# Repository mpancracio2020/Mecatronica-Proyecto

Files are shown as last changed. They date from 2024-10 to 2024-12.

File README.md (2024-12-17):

<!-- Improved compatibility of back to top link: See: https://github.com/othneildrew/Best-README-Template/pull/73 -->

<!--
*** Thanks for checking out the Best-README-Template. If you have a suggestion
*** that would make this better, please fork the repo and create a pull request
*** or simply open an issue with the tag "enhancement".
*** Don't forget to give the project a star!
*** Thanks again! Now go create something AMAZING! :D
-->

<!-- PROJECT SHIELDS -->
<!--
*** I'm using markdown "reference style" links for readability.
*** Reference links are enclosed in brackets [ ] instead of parentheses ( ).
*** See the bottom of this document for the declaration of the reference variables
*** for contributors-url, forks-url, etc. This is an optional, concise syntax you may use.
*** https://www.markdownguide.org/basic-syntax/#reference-style-links
-->

# Mecatronica-Proyecto
<!-- [![Contributors][contributors-shield]][contributors-url]
[![Forks][forks-shield]][forks-url]
[![Stargazers][stars-shield]][stars-url]
[![Issues][issues-shield]][issues-url]
[![MIT License][license-shield]][license-url]
[![LinkedIn][linkedin-shield]][linkedin-url]

 -->

<!-- PROJECT LOGO -->
<br />
<div align="center">
  <a href="https://github.com/othneildrew/Best-README-Template">
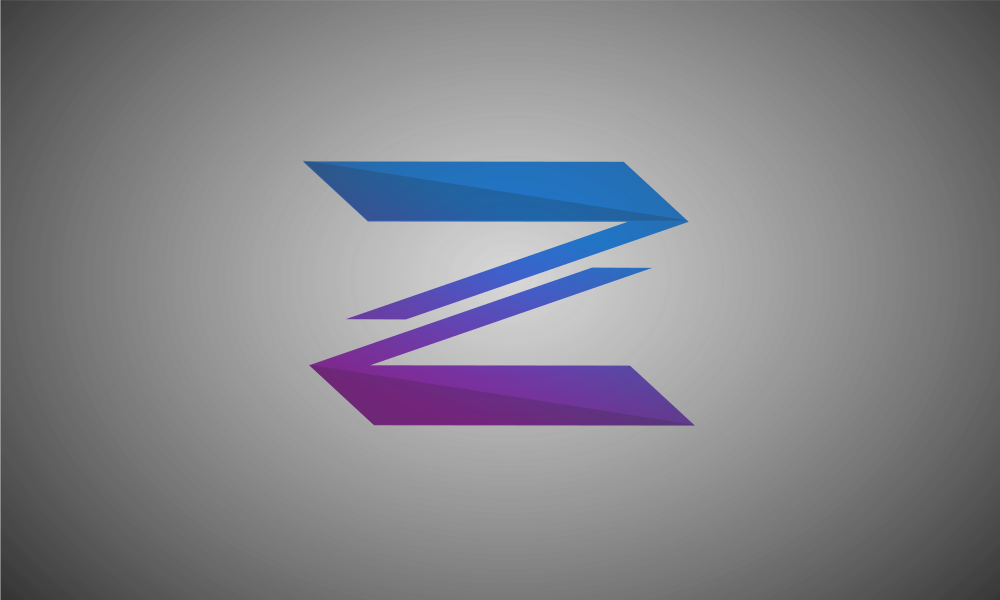
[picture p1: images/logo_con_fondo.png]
    
  </a>

  <h3 align="center">Proyecto-Zeus.</h3>

  <p align="center">
    <br />
    <a href="https://github.com/RoboTech-URJC/Mano-Zeus.git"><strong>Original Robotech Repo »</strong></a>
    <br />
    <br />
    <a href="https://github.com/othneildrew/Best-README-Template">View Demo</a>
    ·
    <a href="https://github.com/othneildrew/Best-README-Template/issues/new?labels=bug&template=bug-report---.md">Personal Blog</a>
  </p>
</div>

---
## **Índice**
1. [Diseño 2D](#id1)
2. [Diseño 3D](#id2)
3. [Diseño Electrónico de la Mano de Zeus](#id3)
4. [Montaje de la Mano de Zeus](#id4)
5. [Código de la Mano de Zeus](#id5)

<div id='id1' />

## Diseño 2D

En estas sesiones nos centramos en el diseño 2D. He aplicado los conocimientos en clase para diseñar un pequeño logo que decore el proyecto.
Requisitos:
* Inkscape.
* Creatividad.

<div align="center">
  <a>
    
  </a>

</div>

A continuacion os dejo un pequeño video de como Marvin ha hecho este pequeño logo sobre el proyecto: 

https://github.com/user-attachments/assets/d4b07c5d-308e-4ce0-a138-df33238a739b

Empleando Inkspace he desarrollado un dibujo de la estructura que debe de tener la mano robótica que vamos a recrear. Es un diseño simple a modo de entendimiento de las diferentes partes que la componen. 

Este es el diseño que hemos obtenido:

<div align="center">
  <a>
    Mano_svg
  </a>

</div>

<p align="right">(<a href="#readme-top">inicio</a>)</p>

En materia del diseño vectorial, también es posible compatibilizarlo con otras técnicas, y para aplicarlo también al proyecto desde otra perspectiva, se me ha ocurrido investigar conversores de gráficos. Existen numerosos convertidores online gratuitos y algunos otros de pago que mejoran los resultados, y esto facilita que ciertas imágenes o diseños puedan ser vectorizados con herramientas también distintas a Inkscape y que no están pensadas en un principio para el diseño vectorial.

Aplicando estas herramientas a nuestro proyecto, Moisés ha diseñado un dibujo simple de algunos componentes de la mano, que también puede servir de apoyo a diagramas explicativos o información que se quiera enseñar y explicar del proyecto:

<p align="center">
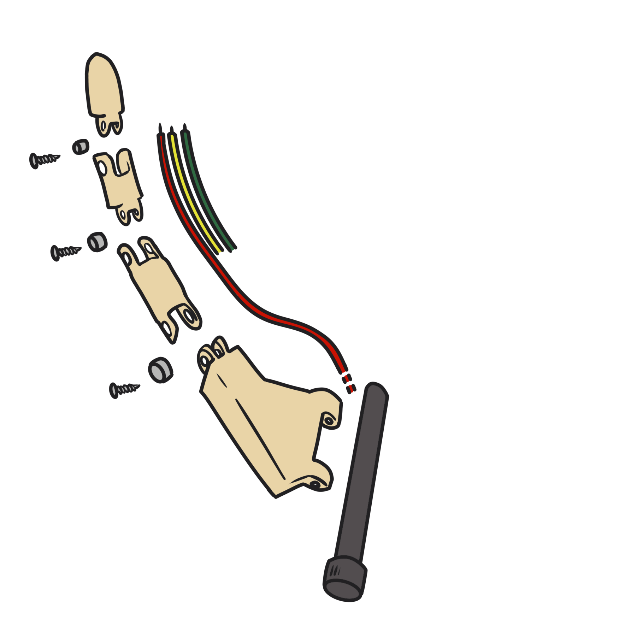
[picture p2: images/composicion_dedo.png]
Alt Imagen 1
  
  Alt Imagen 2
</p>

De las dos imágenes superiores, la izquierda pertenece a un formato en .png, siendo el fichero de dibujo original. Por otra parte la imagen derecha es el resultado de pasar la anterior por un conversor a svg (formato vectorial). El utlizado en este caso ha sido:
- https://png2svg.com/es/

Dejo a continuación un vídeo del proceso de diseño original de la imagen superior, en un programa de diseño no vectorial:

Time-lapse

<div id='id2' />

## **Diseño 3D**

### Mano de Zeus

En cuanto al diseño en 3D que hemos implementado en FreeCad ha sido una estructura simple del ejemplo de dibujo en 2D de Inkspace, obteniendo una estructuracompuesta por rectangulos similar a una mano, pero bastante simplificada. Mostrando en ella todos las piezas en las que tenemos pensado estructurarla.

La estructura se encuentra en el siguiente link: [Mano.FCStd](https://github.com/mpancracio2020/Mecatronica-Proyecto/tree/main/images/Mano.FCStd)

Sin embargo, este modelo 3D era una simplificación del modelo real que queríamos crear y estaba bastante lejos de la complejidad del modelo real que utilizamos. Por lo tanto, me propuse simular una versión más realista del modelo impreso utilizando sus dimensiones para crear un modelo 3D más simple que todos puedan usar y modificar según sus necesidades.

Creé este modelo en FreeCAD utilizando la herramienta "Part" para el diseño 3D general y la herramienta "TechDraw" para elaborar el plano y extraer las medidas.

Aquí están algunas imágenes del modelo que desarrollé, el cual es más similar al real y abarca únicamente la parte de la mano, incluyendo los huecos para pasar los hilos y mover los dedos. La muñeca y el antebrazo no están diseñados.

<p align="center"> 
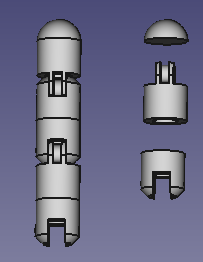
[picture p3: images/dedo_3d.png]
   
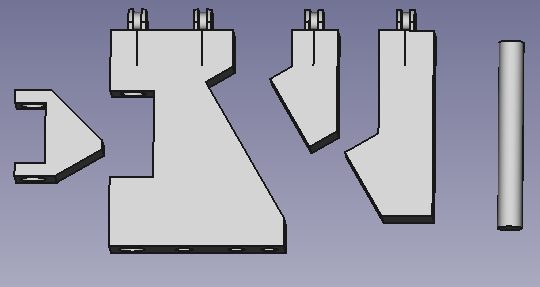
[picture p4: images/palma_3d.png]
   
</p> 
<p align="center"> 
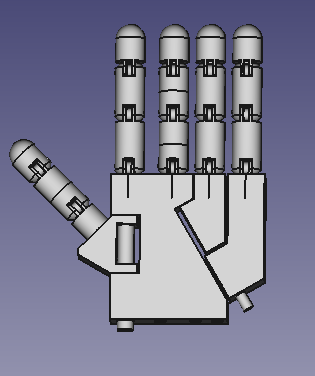
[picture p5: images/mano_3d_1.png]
   
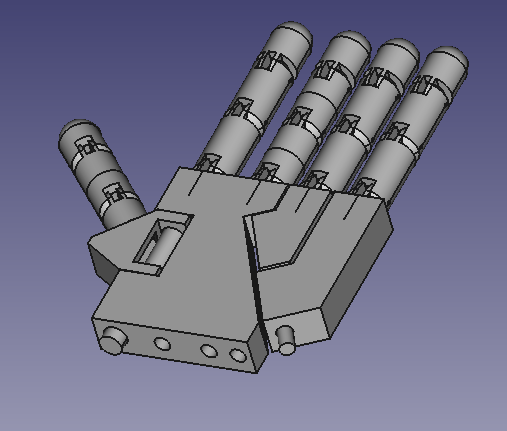
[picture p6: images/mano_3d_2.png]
  
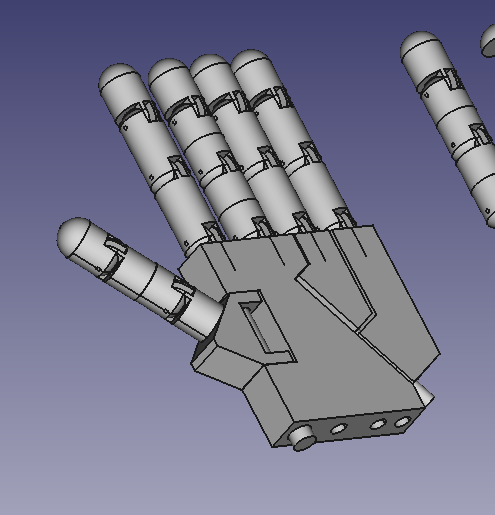
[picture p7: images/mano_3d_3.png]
   
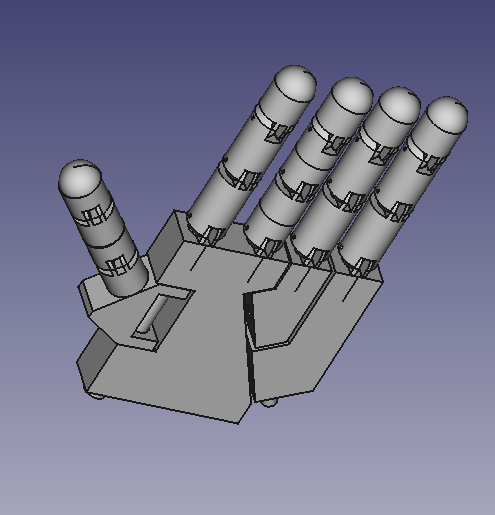
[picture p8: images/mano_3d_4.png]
   
</p>

Este es un video del diseño final.

<p align="center"> 
   
</p>

Los planos de las piezas son los siguiente:

- Dedo:
<p align="center"> 
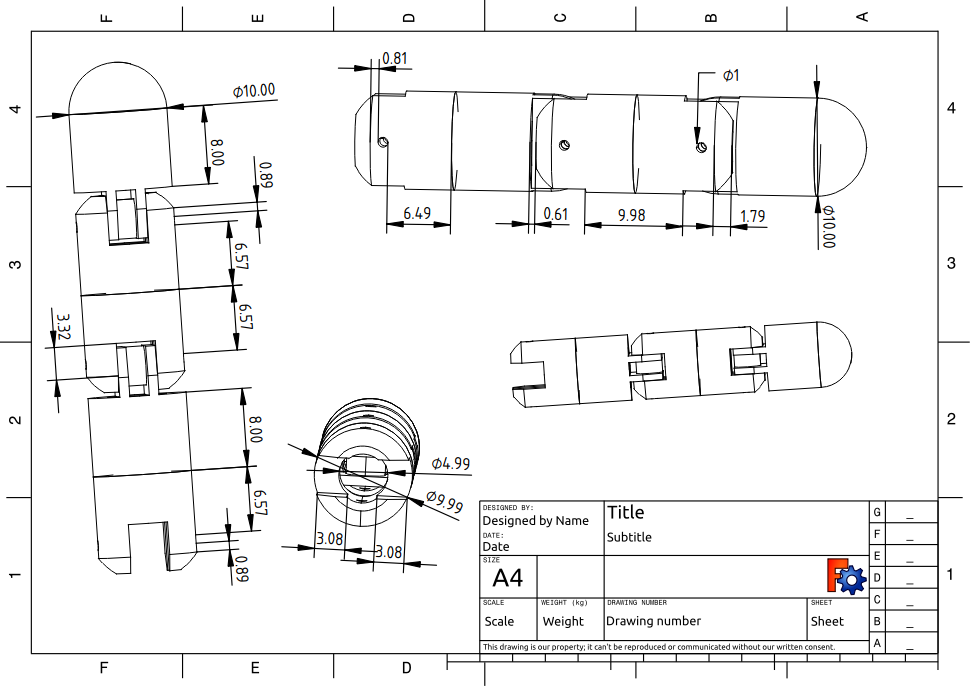
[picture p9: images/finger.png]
   
   
</p>

- Pulgar:
<p align="center">
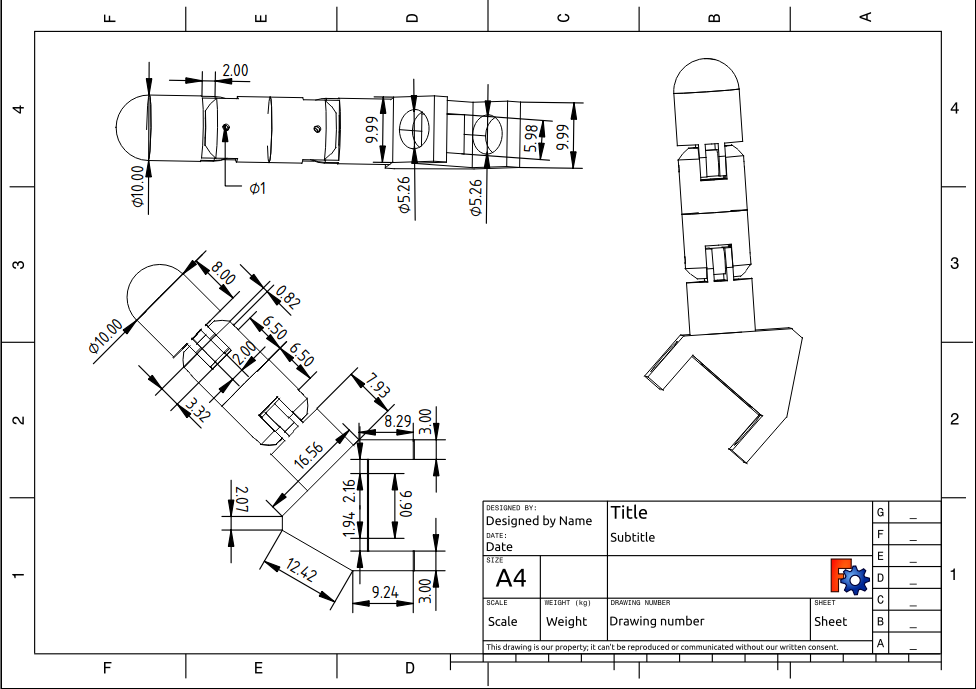
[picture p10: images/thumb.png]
   
   
</p>

- Palma:
<p align="center">
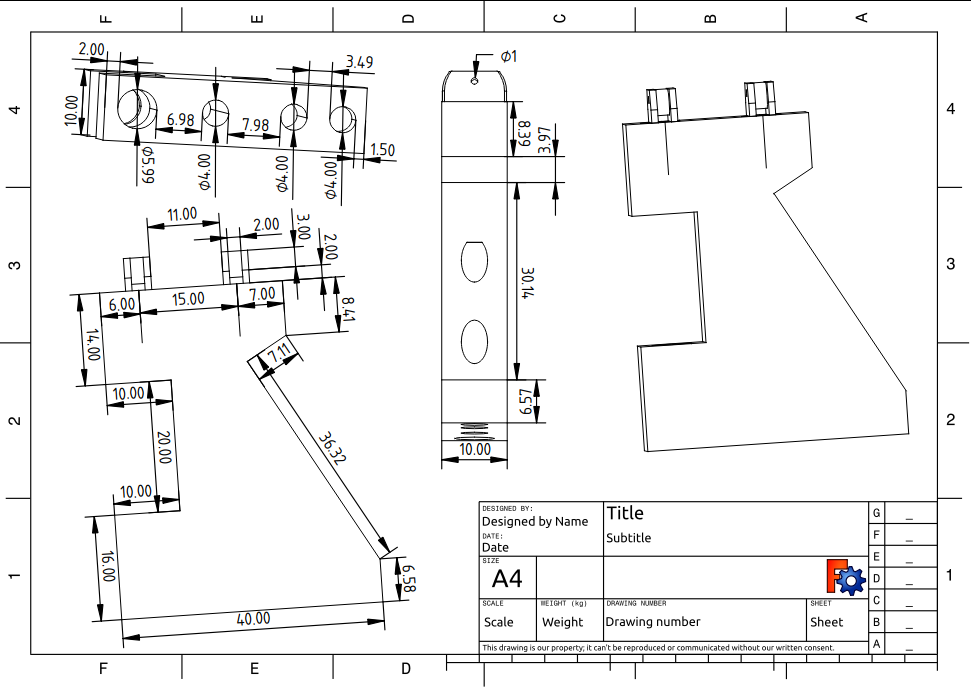
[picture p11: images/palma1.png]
   
   
</p>

- Palma anular:
<p align="center">
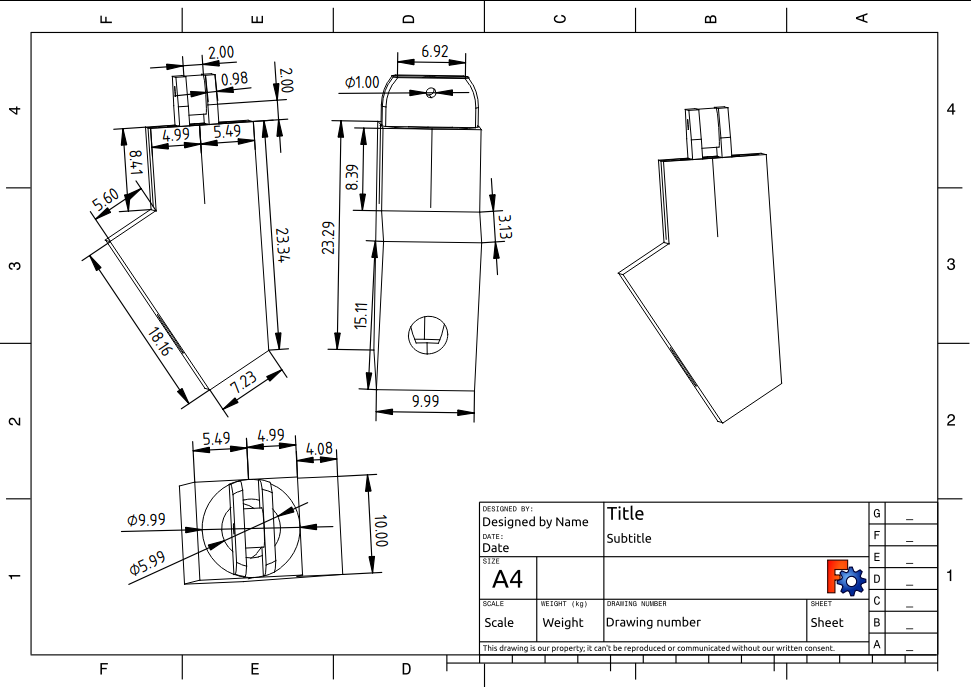
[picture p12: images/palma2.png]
   
   
</p>

- Palma meñique:
<p align="center">
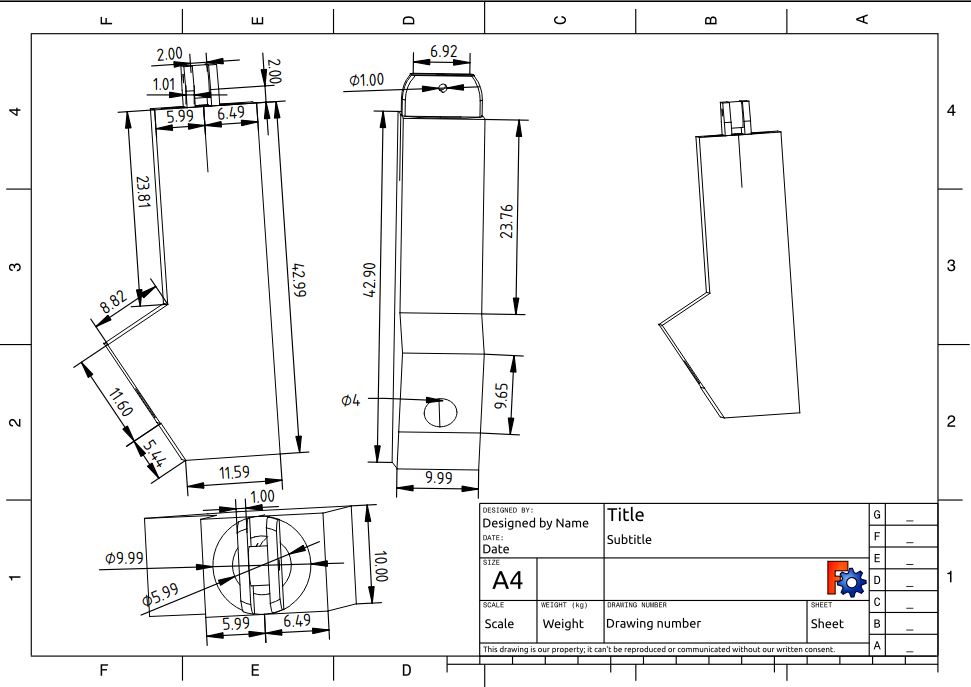
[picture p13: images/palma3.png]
   
   
</p>

- Mano en general:
<p align="center">
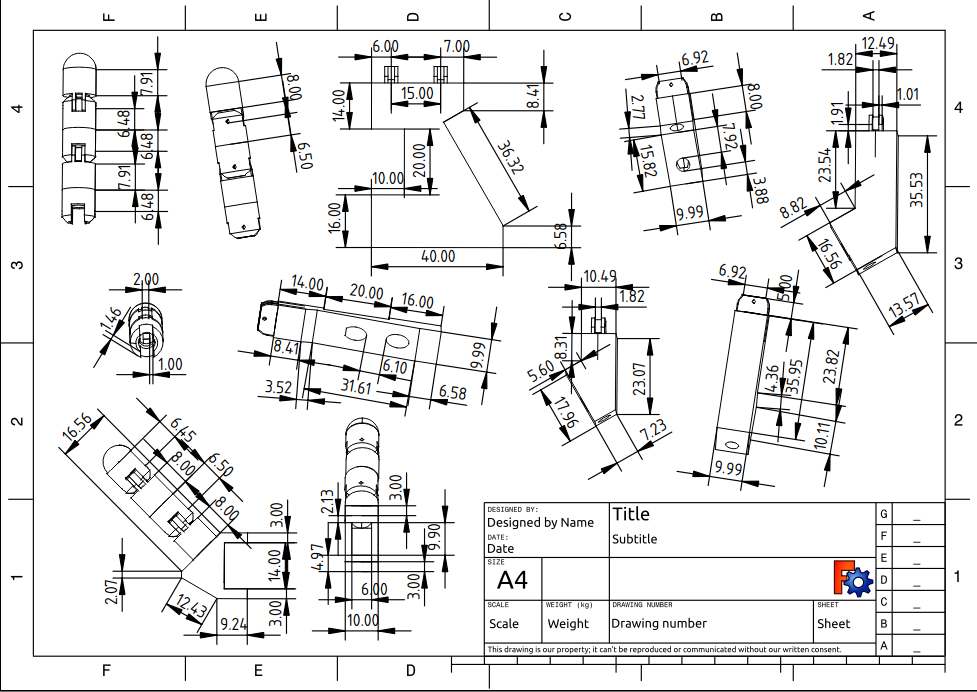
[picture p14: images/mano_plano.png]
   
   
</p>

Y el archivo con todo el diseño 3D lo puedes encontrar en [hand.FCStd](https://github.com/mpancracio2020/Mecatronica-Proyecto/tree/main/images/hand.FCStd)

En cuanto al resto de diseño 3D hemos utilizado Ultimaker Cura para diseñar las piezas basandonos en el proyecto original del cual hemos sacado la idea. Hemos modificado los archivos (.lts) de los componentes aportando diferentes valores para obtener la mejor impresión de las piezas en nuestras impresoras 3D.

### Soporte para el antebrazo

Como parte adicional a la mano de Zeus en sí, decidimos buscar una manera de mantenerla sujeta sin necesidad de apoyarla directamente sobre la mesa, o de sujetarla para cualquier tipo de demostración y presentación. Esto nos llevó a pensar en un soporte que se adaptase a la forma del antebrazo y nos permitiera mantenerlo en posición horizontal, ya que podría ser algo desarrollado en una sola pieza, y más sencillo que un soporte que la mantuviera en vertical a la hora de hacer el diseño. Además, esta posición también resulta más segura, ya que reduce casi al mínimo la posibilidad de que pudiera caerse el conjunto.

Para el soporte, tomando de base un fichero stl, aplicamos ciertas modificaciones realizadas con blender para adaptarlo a nuestras necesidades de tamaño, número de caras y vértices, forma, etc. Las modificaciones aplicadas fueron realizadas utilizando Blender 2.79b, una versión que inicialmente dificulta la compatibilidad con stl, pero que haciendo uso de dos plugins sirvió para aquello que necesitábamos. Dichos plugins quedan a continuación para su descarga y utilización en esta misma versión o similares:

- [blender2ogre.zip](./add-ons/blender2ogre-0.6.0.zip)
- [ImportExporTL-blender.zip](./add-ons/ImportExportTL_blender25x_v0.6.2.zip)

Cualquiera que quiera replicar la utilización debe descargar los ficheros previos como zip, sin extraer su contenido y añadirlos tal cual en el apartado de *"Add-ons"* dentro de la pestaña de *"User Preferences"* en el editor de Blender. Una vez hecho esto, cualquier problema de compatibilidad con ficheros stl debería quedar resuelto, tanto para importar como para exportar este tipo de ficheros.

#### Desarrollo en blender

El desarrollo de nuestra versión final del soporte se hizo aplicando al stl original un ajuste leve en su tamaño, junto a una reducción de la carga de vértices y caras que presentaba la figura original. Finalmente tras dejar una versión final que encajaba con aquello que buscábamos, re-exportamos el trabajo a stl para poder posteriormente tomar las medidas pertinentes en FreeCad del soporte hecho.

<p align="center">
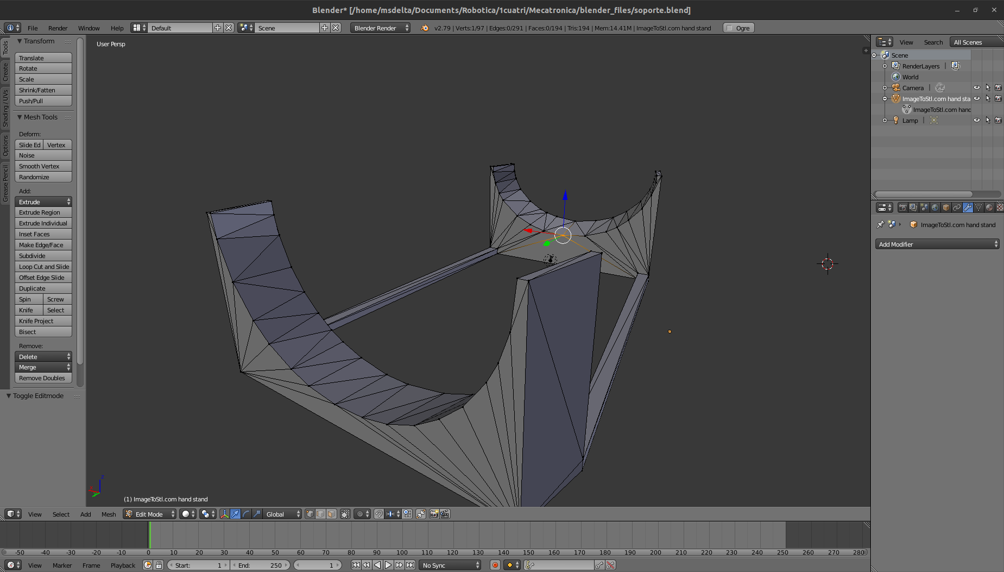
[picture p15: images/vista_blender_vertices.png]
  
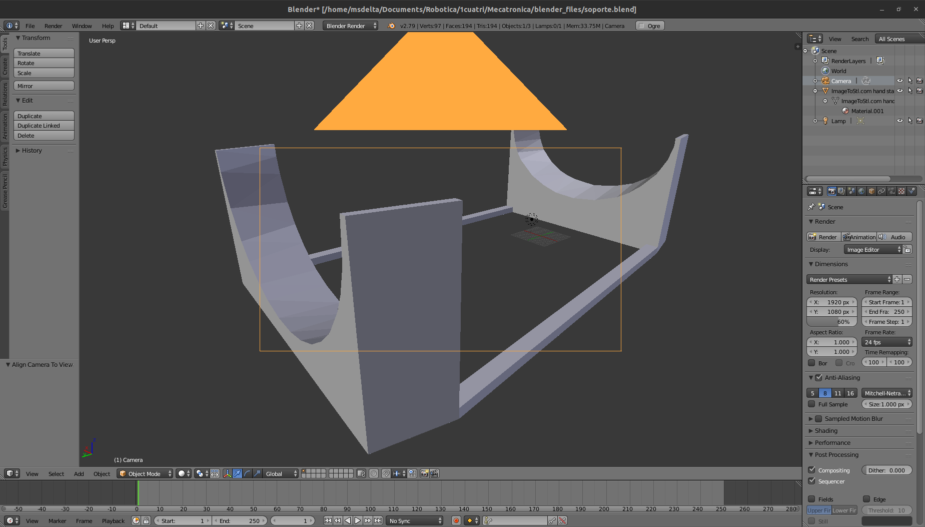
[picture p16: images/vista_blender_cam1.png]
  
</p>

A continuación queda el fichero de blender en su versión final para su copia y libre utilización:

- [Soporte_redu_blend](./models/soporte_redu.blend)

Además de su modelado y ajustado, tratamos de realizar un renderizado del mismo para una mejor presentación y previsualización del resultado final, pero por ciertos problemas con la edición del enfoque de la cámara y los tamaños empleados en edición, no fuimos capaces de lograr un resultado aceptable. Pese a ello, quedan arriba añadidas unas imágenes tomadas del proceso y del modelo visualizado en blender usando distintos modos. Además de las imágenes siguientes, tomadas mientras se intentaba realizar y configurar el renderizado:

<p align="center">
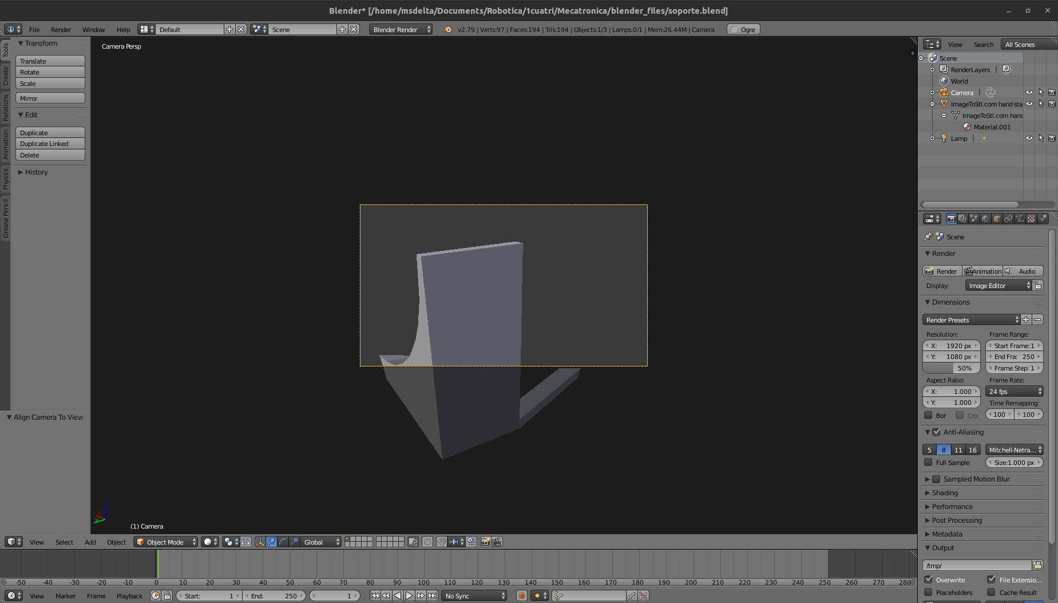
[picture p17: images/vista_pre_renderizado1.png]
  
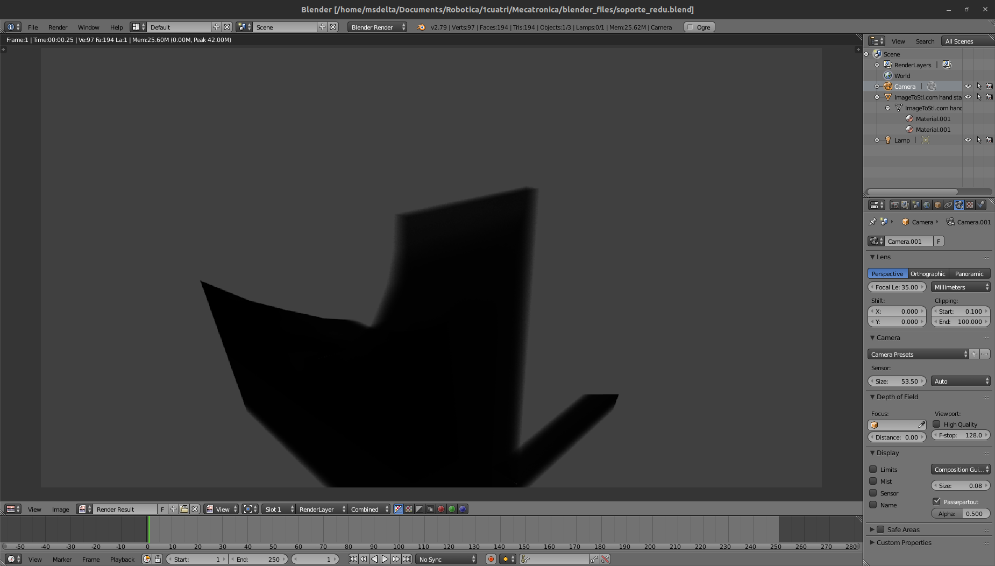
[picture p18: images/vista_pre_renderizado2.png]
  
</p>

Por otro lado, también queda a continnuación el fichero final logrado en formato .stl también para su libre utilización y modificación:

- [Soporte_redu_stl](./models/soporte_redu.stl)

#### Vistas y medidas del soporte

Partiendo del modelo stl logrado finalmente, usamos FreeCad para tomar ciertas medidas del mismo y corroborar su validez, así como para sacar ciertos planos y vistas del mismo.

Dado que el modelo no es simétrico, y tiene algunas irregularidades, por tener que adaptarse necesariamente al antebrazo de la Mano de Zeus, hay ciertas medidas que resultan poco intuitivas y puede creerse que son erróneas, pero si comprobamos todas las vistas y nos fijamos en la orientación de las caras laterales, podemos ver que realmente las medidas son las correctas. 

<p align="center">
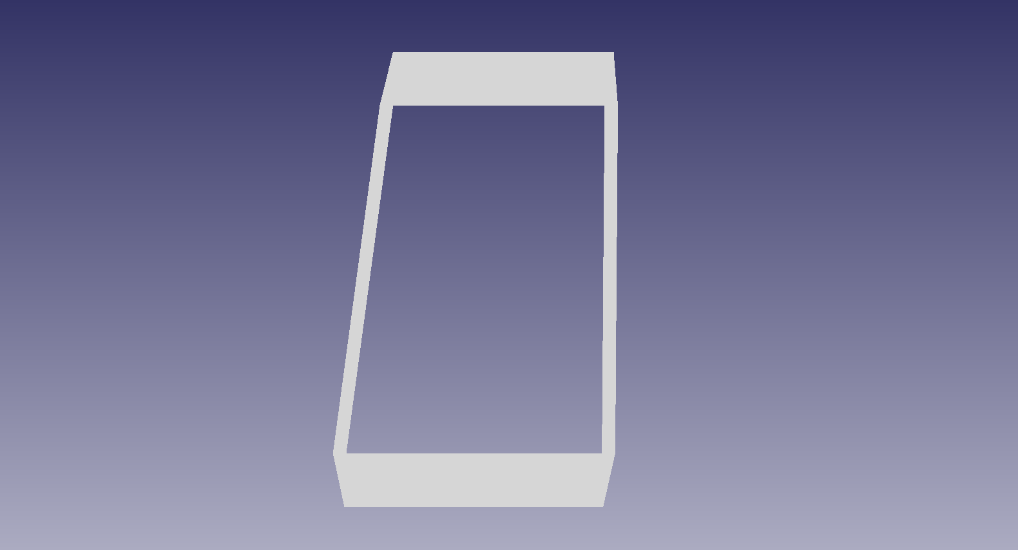
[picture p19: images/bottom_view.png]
bottom_view
  
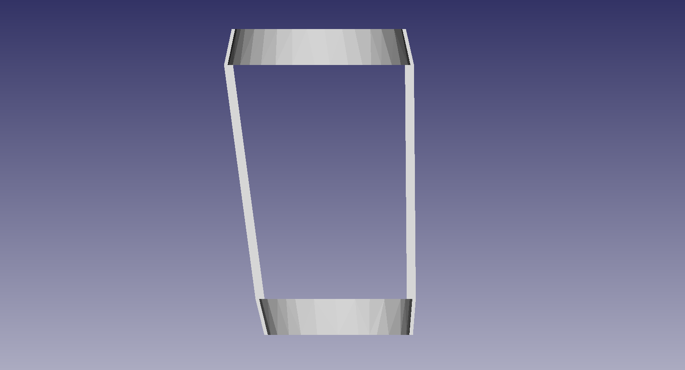
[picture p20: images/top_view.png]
top_view
  
</p>

<p align="center">
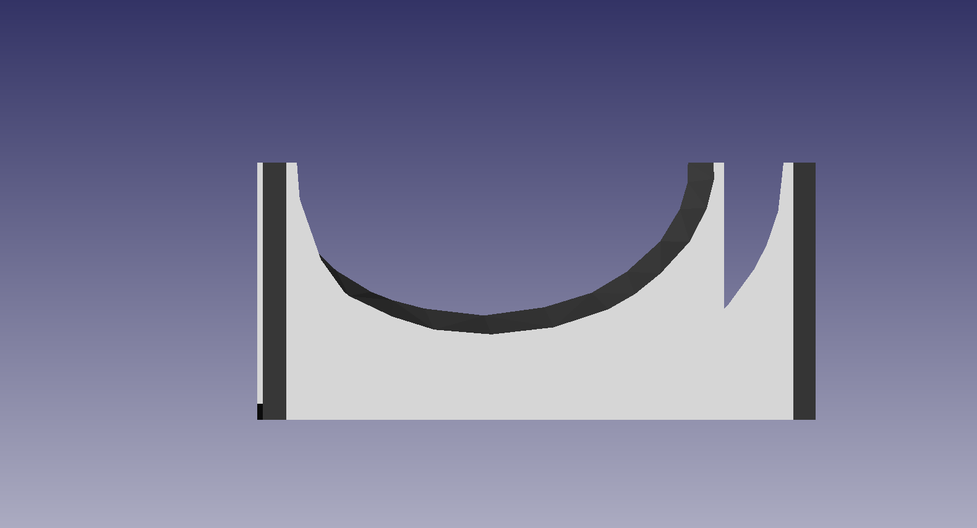
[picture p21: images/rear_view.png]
rear_view
  
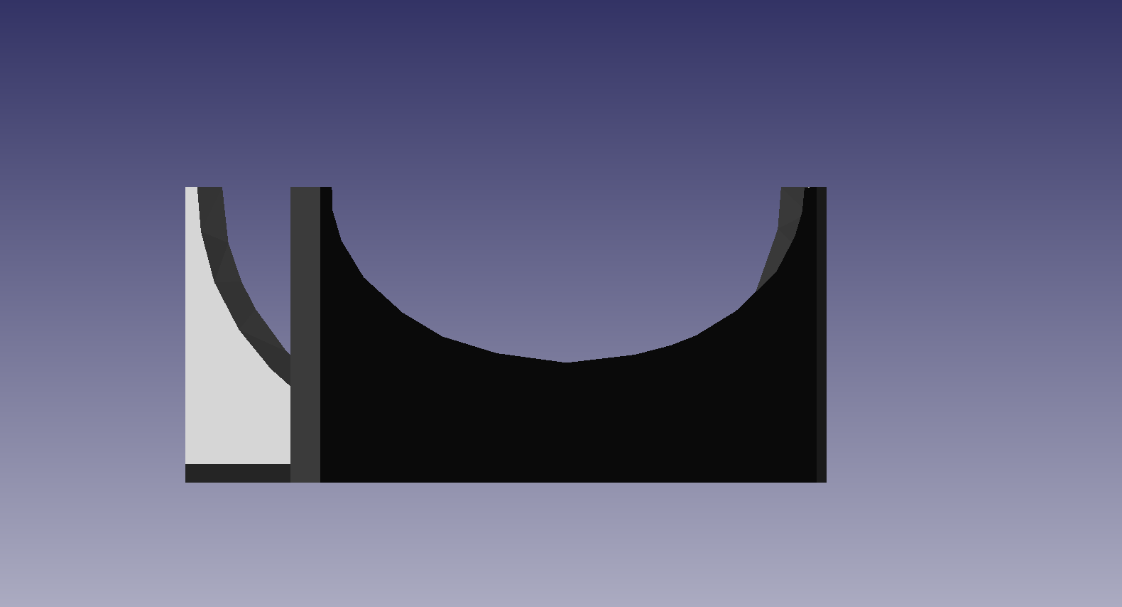
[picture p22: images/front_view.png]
front_view
  
</p>

Las dos imágenes superiores muestran la vista desde la parte inferior y superior (bottom y top) respectivamente de izquierda a derecha, y en igual orden podemos ver las vistas desde la parte trasera y delantera (rear y front) en las imágenes inferiores.

Si comparamos y observamos detenidamente la orientación de los canales laterales que unen los dos arcos sobre los que se apoya finalmente el antebrazo, podemos ver que la pieza carece de simetría, y unido esto a que en las vistas superior e inferior observamos los laterales en detalle, viéndose que no conforman rectas perfectas, facilita la posterior comprensión de las medidas tomadas y las leves irregularidades que parecen presentar en un comienzo.

#### Mediciones laterales

Adicionalmente a lo anterior, dejamos a continuación dos imágenes con las medidas que más dificultad de comprensión pueden tener, las laterales. Estas medidas fueron tomadas de forma persistente usando la función de regla en FreeCad, y pueden servir como idea previa a la visualización de los planos completos finales de la pieza, para hacerse una idea del tamaño y verificar sus dimensiones:

<p align="center">
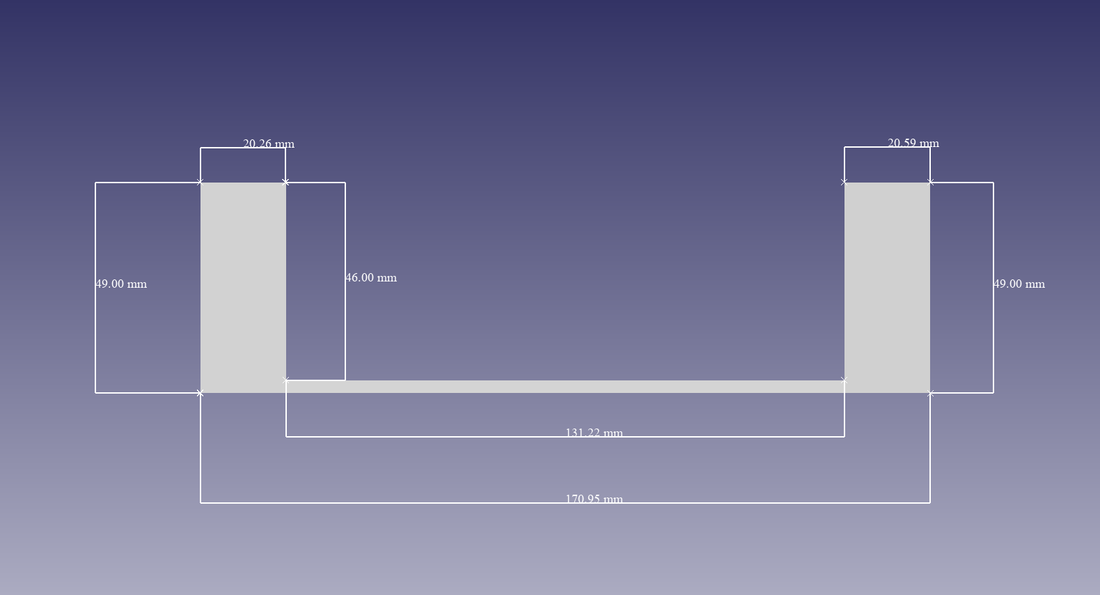
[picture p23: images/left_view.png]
rear_view
  
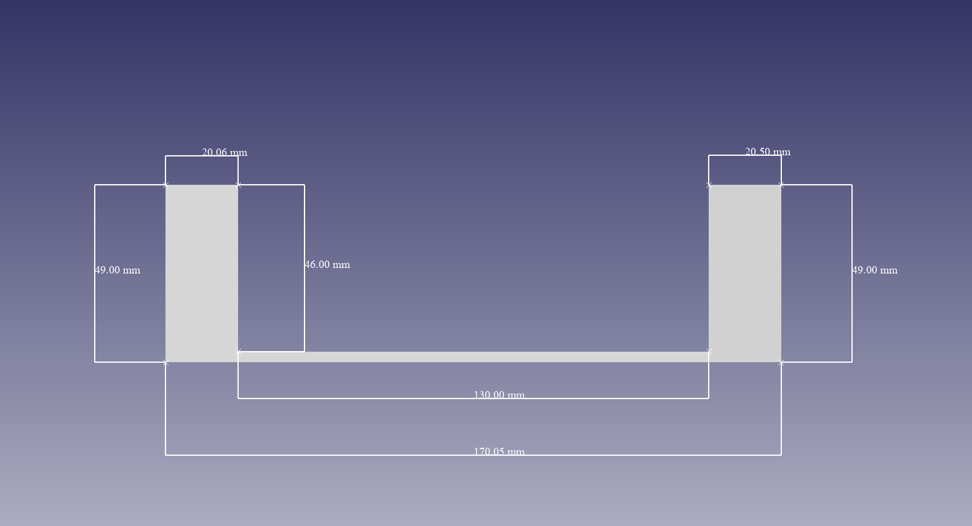
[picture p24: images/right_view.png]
front_view
  
</p>

La imagen izquierda muestra una vista tomada del lado izquierdo del soporte, con las medidas de sus caras más relevantes indicadas en la propia imagen. De igual manera, la imagen derecha muestra la misma información pero relativa a la vista lateral derecha del modelo. 

Y como un extra más a estas imágenes podemos ver una perspectiva diferente que muestra las medidas de ambos lados en una visualización unificada. La imagen inferior está orientada de manera evidencial a las medidas, correspondiendo aquellas en el lado derecho de la imagen con las medidas del lateral derecho:

<p align="center">
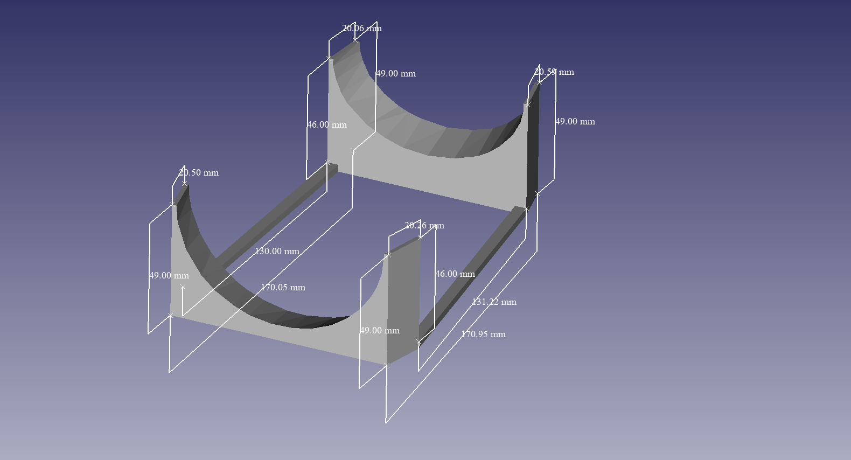
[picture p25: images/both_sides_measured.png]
  
</p>

También queda a continuación el proyecto de FreeCad que hemos empleado para estas mediciones rápidas y explicación de las mismas:

- [Soporte_redu_fcstd](./models/soporte_redu.FCStd)

<p align="center">
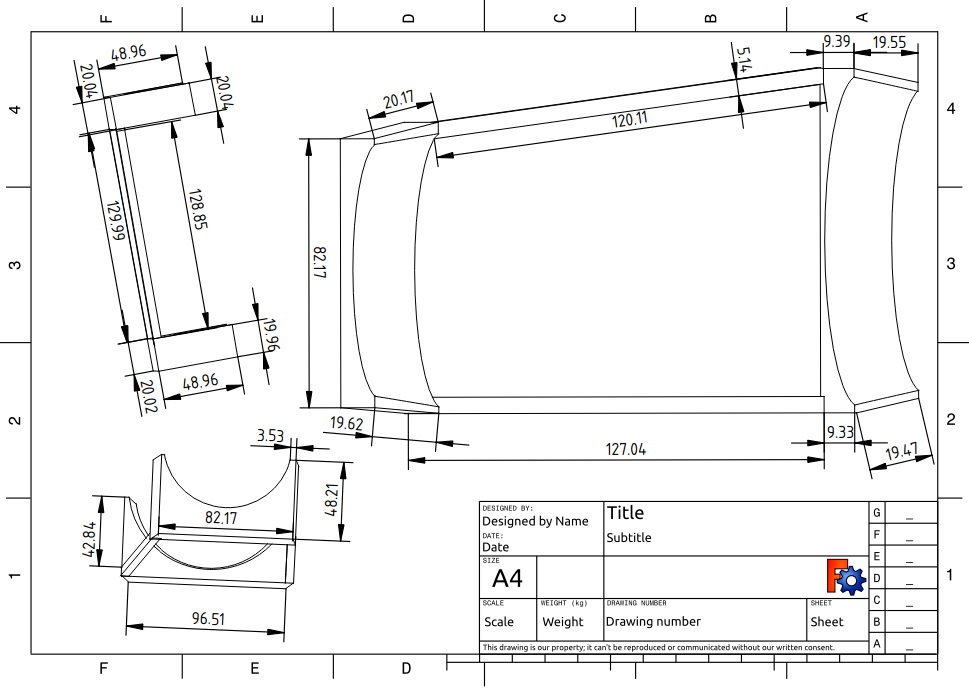
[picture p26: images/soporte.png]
  
  
</p>

<div  id='id3' /> 

## **Diseño Electrónico de la Mano de Zeus**

### Componentes:
Para crear y diseñar el circuito electronico primero debemos elegir que componentes son necesarios y los más óptimos para el correcto funcionamiento de la mano.

- **Arduino UNO / MEGA:** primero hemos elegido como cerebro de nuestro robot un arduino UNO ya que es suficiente para poder comandar el resto de componentes. Si se llega a aumentar el numero de componentes como el añadir otro brazo, usaremos un arduino Mega para poder tener mas pines a los que conectar todos los componentes.

<div align="center">
  <a>
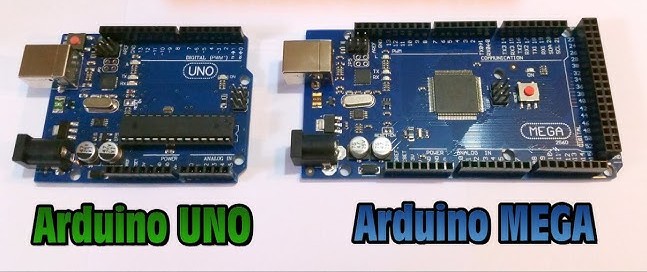
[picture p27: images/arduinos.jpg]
    
  </a>

</div>

- **Servos:** en concreto el modelo tower pro mg996r, un servo de 360 grados el cual nos permite una rotación completa y necesaria para mover los dedos y muñeca los ángulos necesarios. En concreto usaremos 6 servos por cada mano.

<div align="center">
  <a>
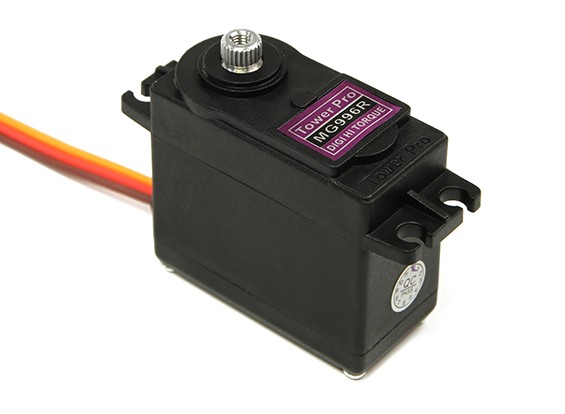
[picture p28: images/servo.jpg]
    
  </a>

</div>

- **Protoboard:** la usaremos para tener mejor conectados y controlados todos los componentes.
- **Cables Macho-Macho / Macho-Hembra:** los usaremos para conectar los componentes entre sí.
- **Batería:** la necesitaremos implementar también para poder mover los servos y que estos puedan mover los dedos.
<div align="center">
  <a>
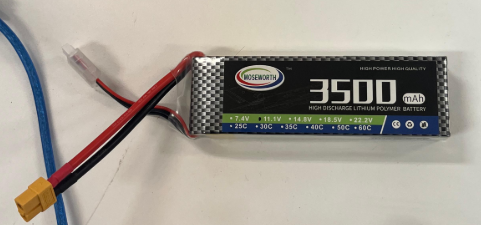
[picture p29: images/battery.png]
    
  </a>
</div>

### Circuito (Fritzing):
Para poder visualizar de una manera mas simple y rapida sin tener que conectar de forma presencial todo el circuito hemos usado la aplicación Fritzing para poder diseñar el circuito. Esta nos permite añadir los componentes necesarios y los modelos específicos que utilizaremos.

El circuito inicial diseñado es el siguiente:

<div align="center">
  <a>
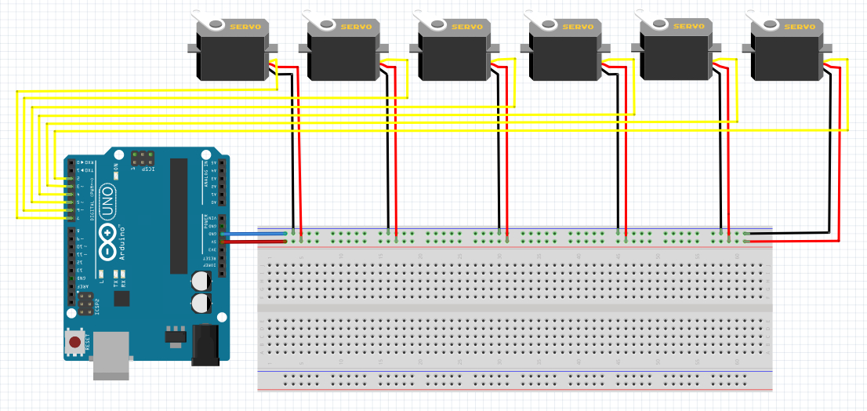
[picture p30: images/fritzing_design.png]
    
  </a>

</div>

Después de probar este circuito nos dimos cuenta de que los servos se movian pero no tenían la fuerza necesaria para poder mover los dedos tirando de los hilos, debido a su peso. Por lo cual se nos ocurrió posteriormente el incluir una batería solo para alimentar a todos los servos. Después de añadirla el circuito diseñado queda de la siguiente forma:

<div align="center">
  <a>
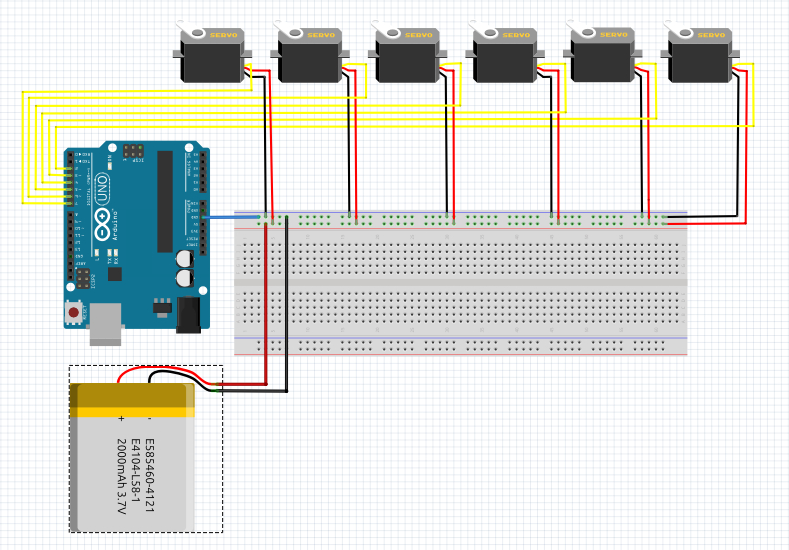
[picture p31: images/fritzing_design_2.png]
    
  </a>

</div>

<div  id='id4' /> 

## Montaje de la Mano de Zeus

### Componentes:

Teniendo el diseño 3d de las piezas, ajustamos adecuadamente los tamaños y utilizamos una impresora 3d para imprimir cada una. En total para la mano derecha desarrollada fueron utilizadas las siguientes partes:
- **Dedo meñique:** conformado por 6 piezas, ensambladas posteriormente entre sí. Adaptado del modelo original: [auriculaire-finger](https://inmoov.fr/inmoov-stl-3d/?bodyparts=Right-Hand&parts=Auriculaire3.stl)
- **Dedo anular:** conformado por 6 piezas, ensambladas posteriormente entre sí. Adaptado del modelo original: [ring-finger](https://inmoov.fr/inmoov-stl-3d/?bodyparts=Right-Hand&parts=ringfinger3.stl)
- **Dedo corazón:** conformado por 6 piezas, ensambladas posteriormente entre sí. Adaptado del modelo original: [majeure-finger](https://inmoov.fr/inmoov-stl-3d/?bodyparts=Right-Hand&parts=Majeure3.stl)
- **Dedo índice:** conformado por 6 piezas, ensambladas posteriormente entre sí. Adaptado del modelo original: [index-finger](https://inmoov.fr/inmoov-stl-3d/?bodyparts=Right-Hand&parts=Index3.stl)
- **Dedo pulgar:** conformado por 6 piezas, ensambladas posteriormente entre sí. Adaptado del modelo original: [thumb-finger](https://inmoov.fr/inmoov-stl-3d/?bodyparts=Right-Hand&parts=thumb5.stl)

<p align="center">
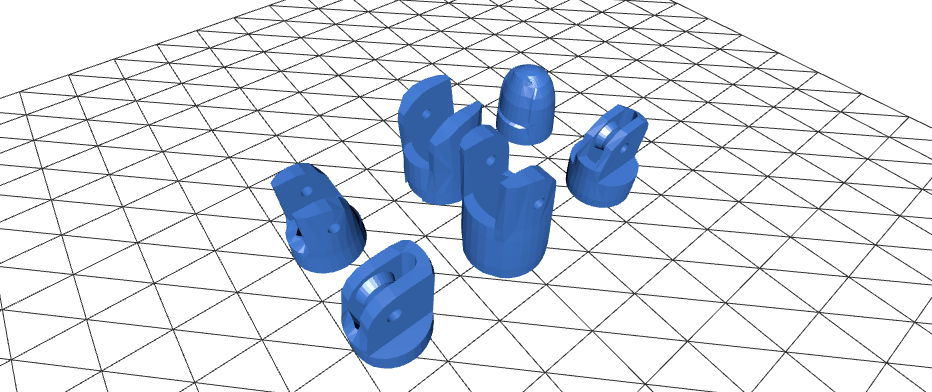
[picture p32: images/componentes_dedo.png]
componentes_dedo
  
</p>

- **Espaciador:** soporte estructural para ensamblar los dedos meñique y anular con la muñeca corta. Adaptado del modelo original: [bolt-entretoise](https://inmoov.fr/inmoov-stl-3d/?bodyparts=Right-Hand&parts=Bolt_entretoise7.stl)
- **Muñeca larga:** pieza única, ensamblada para conformar el mecanismo del movimiento transferido de muñeca a los dedos, junto con la Muñeca corta. Adaptado del modelo original: [wrist-large](https://inmoov.fr/inmoov-stl-3d/?bodyparts=Right-Hand&parts=WristlargeV4.stl)
- **Muñeca corta:** dos piezas, ensambladas al dedo anular y meñique, uniéndolos a la Muñeca larga para conformar el movimiento transferido por la muñeca a los dedos mencionados. Adaptado del modelo original: [wrist-small](https://inmoov.fr/inmoov-stl-3d/?bodyparts=Right-Hand&parts=WristsmallV4.stl)

<p align="center">
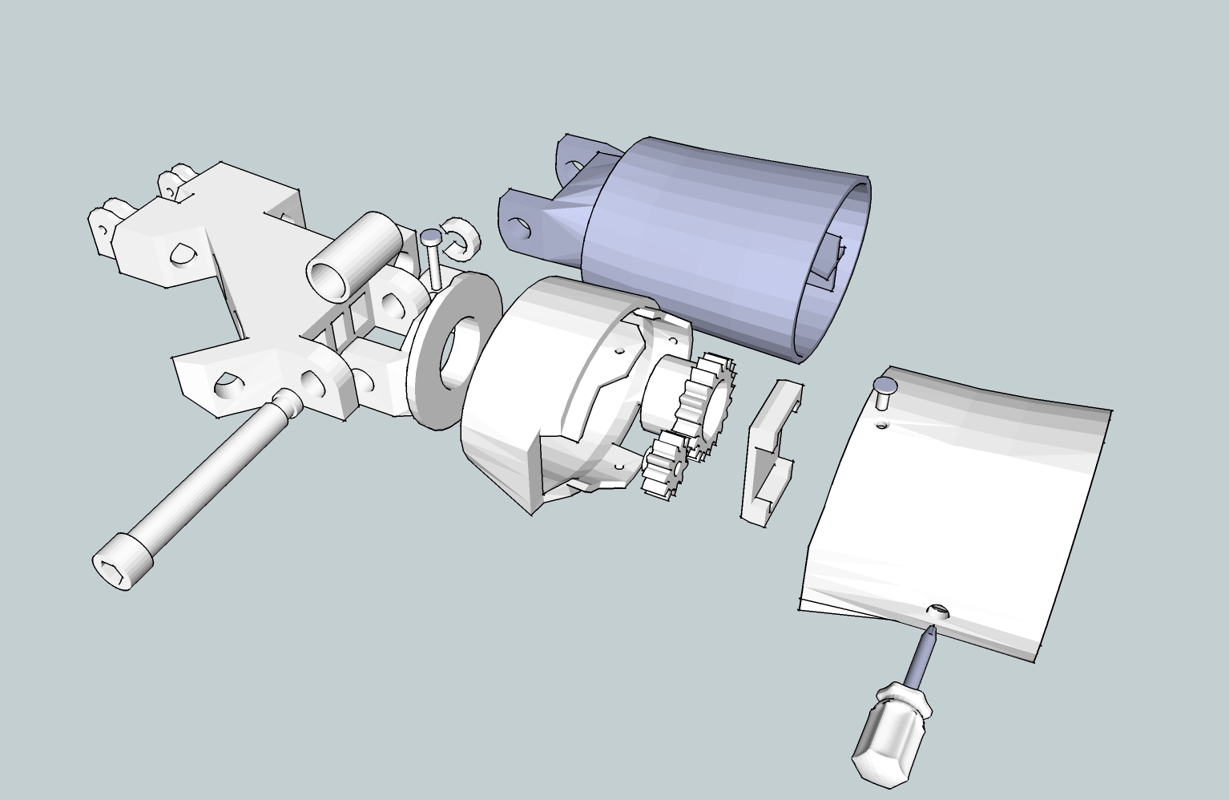
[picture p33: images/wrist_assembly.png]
  
</p>

- **CableHolderWristV5:** elemento de apoyo para facilitar la incorporación del cableado que conecta con muñeca y mano. Adaptado del modelo original: [cable-holder](https://inmoov.fr/inmoov-stl-3d/?bodyparts=Rotation-Wrist&parts=CableHolderWristV5.stl)
- **RotaWrist 3V3:** pieza única relacionada con el módulo de la muñeca. Adaptado del modelo original: [rotawrist3v3](https://inmoov.fr/inmoov-stl-3d/?bodyparts=Rotation-Wrist&parts=RotaWrist3V3.stl)
- **RotaWrist 2V3:** primera de las piezas que conforman la cobertura posterior del módulo de la muñeca. Adaptado del modelo original: [rotawrist2v3](https://inmoov.fr/inmoov-stl-3d/?bodyparts=Rotation-Wrist&parts=RotaWrist2V3.stl)
- **RotaWrist 1V4:** segunda de las piezas que conforman la cobertura posterior del módulo de la muñeca. Adaptado del modelo original: [rotawrist1v4](https://inmoov.fr/inmoov-stl-3d/?bodyparts=Rotation-Wrist&parts=RotaWrist1V4.stl)
- **WristgearsV5:** engranajes necesarios para la rotación del módulo de la muñeca. Adaptado del modelo original: [wrist-gears](https://inmoov.fr/inmoov-stl-3d/?bodyparts=Rotation-Wrist&parts=WristGearsV5.stl)
- **RobocableBackV3:** pieza de apoyo para la integración del cableado, junto con rob-cable-front. Adaptado del modelo original: [rob-cable-back](https://inmoov.fr/inmoov-stl-3d/?bodyparts=Forearm-and-Servo-Bed&parts=RobCableBackV3.stl)
- **RobocableFrontV3v:** segunda pieza de apoyo para la integración del cableado con la rotación de muñeca. Adaptado del modelo original: [rob-cable-front](https://inmoov.fr/inmoov-stl-3d/?bodyparts=Forearm-and-Servo-Bed&parts=RobCableFrontV3.stl)
- **RoboRingV3:** anillos ensamblados a los servomotores, necesarios para implementar el movimiento de los dedos. Adaptado del modelo original: [rob-ring](https://inmoov.fr/inmoov-stl-3d/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)
- **RobServoBedV6:** pieza única empleada para situar correctamente la posición interna de los servomotores. Adaptado del modelo original: [servo-bed](https://inmoov.fr/inmoov-stl-3d/?bodyparts=Forearm-and-Servo-Bed&parts=RobServoBedV6.stl)
- **TensionerRightV1:** pieza de apoyo al ensamblaje de los componentes internos. Adaptado del modelo original: [tensioner-right](https://inmoov.fr/inmoov-stl-3d/?bodyparts=Forearm-and-Servo-Bed&parts=TensionerRightV1.stl)
- **Servo-pulley:** poleas circulares, transforman el movimiento de los servomotores. Adaptado del modelo original: [servo-pulley](https://inmoov.fr/inmoov-stl-3d/?bodyparts=Forearm-and-Servo-Bed&parts=servo-pulleyX5.stl)

<p align="center">
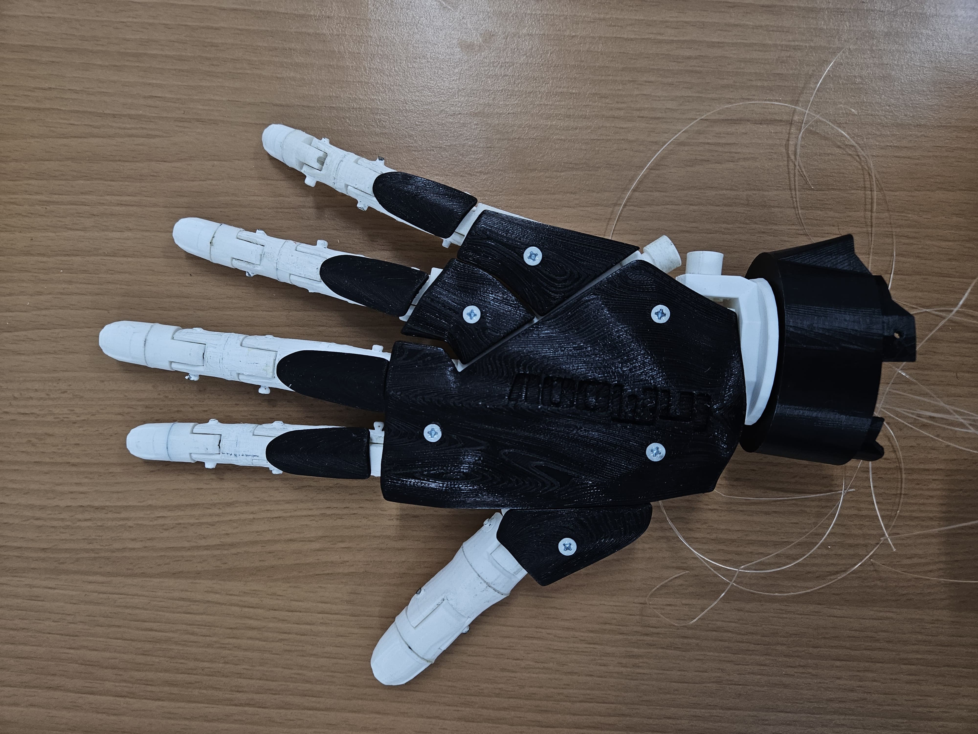
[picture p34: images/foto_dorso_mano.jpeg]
  
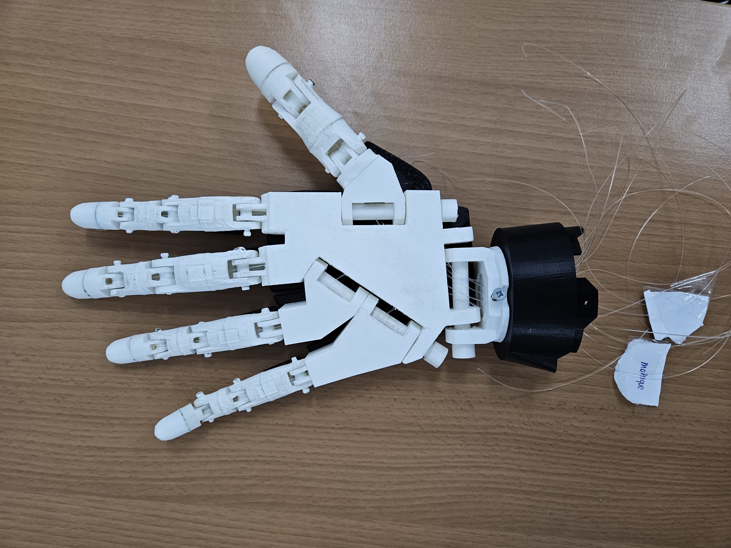
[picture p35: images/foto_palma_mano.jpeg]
  
</p>

- **Cubierta superior (tumbada):** similar a las piezas que cubren los dedos, siendo esta una cobertura para la parte superior de la mano. Adaptado del modelo original: [top-surface](https://inmoov.fr/inmoov-stl-3d/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)
- **Cubrededos:** conformado por 5 piezas, ensambladas sobre los dedos. Adaptado del modelo original: [cover-finger](https://inmoov.fr/inmoov-stl-3d/?bodyparts=Right-Hand&parts=coverfinger1.stl)
- **Soporte Arduino:** pieza única para contener la placa Arduino controladora. Adaptado del modelo original: [arduino-support](https://inmoov.fr/inmoov-stl-3d/?bodyparts=Right-Hand&parts=ardiuinosupport.stl)
- **Robcap3V2:** uno de los componentes que conforman el antebrazo, siendo la cubierta superior del mismo. Adaptado del modelo original: [robcap3v2](https://inmoov.fr/inmoov-stl-3d/?bodyparts=Right-Hand&parts=robcap3V2.stl)
- **Robcap2V4:** primera cubierta anterior del antebrazo. Adaptado del modelo original: [robcap2v4](https://inmoov.fr/inmoov-stl-3d/?bodyparts=Right-Hand&parts=robpart2V4.stl)
- **Robcap3V4:** segunda cubiera anterior del antebrazo. Adaptado del modelo original: [robcap3v4](https://inmoov.fr/inmoov-stl-3d/?bodyparts=Right-Hand&parts=robpart3V4.stl)
- **Robcap4V4:** primera cubierata posterior del antebrazo. Adaptado del modelo original: [robcap4v4](https://inmoov.fr/inmoov-stl-3d/?bodyparts=Right-Hand&parts=robpart4V4.stl)
- **Robcap5V4:** segunda cubierta posterior del antebrazo. Adaptado del modelo original: [robcap5v4](https://inmoov.fr/inmoov-stl-3d/?bodyparts=Right-Hand&parts=robpart5V4.stl)

<p align="center">
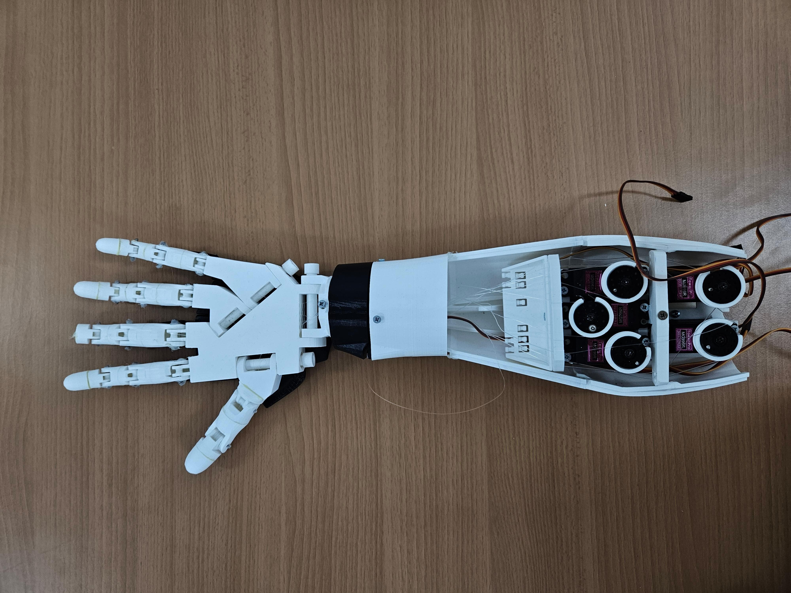
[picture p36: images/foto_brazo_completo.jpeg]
  
</p>

### **Diseño esquemático por componentes**

Para simplificar el montaje, y describir de manera más sencilla la forma en que se realizó, queda a continuación un diagrama dibujado y comentado, con sus elementos explicados en detalle más adelante en este mismo documento:

<div style="display: flex; align-items: left;">

<div style="flex: 1;">
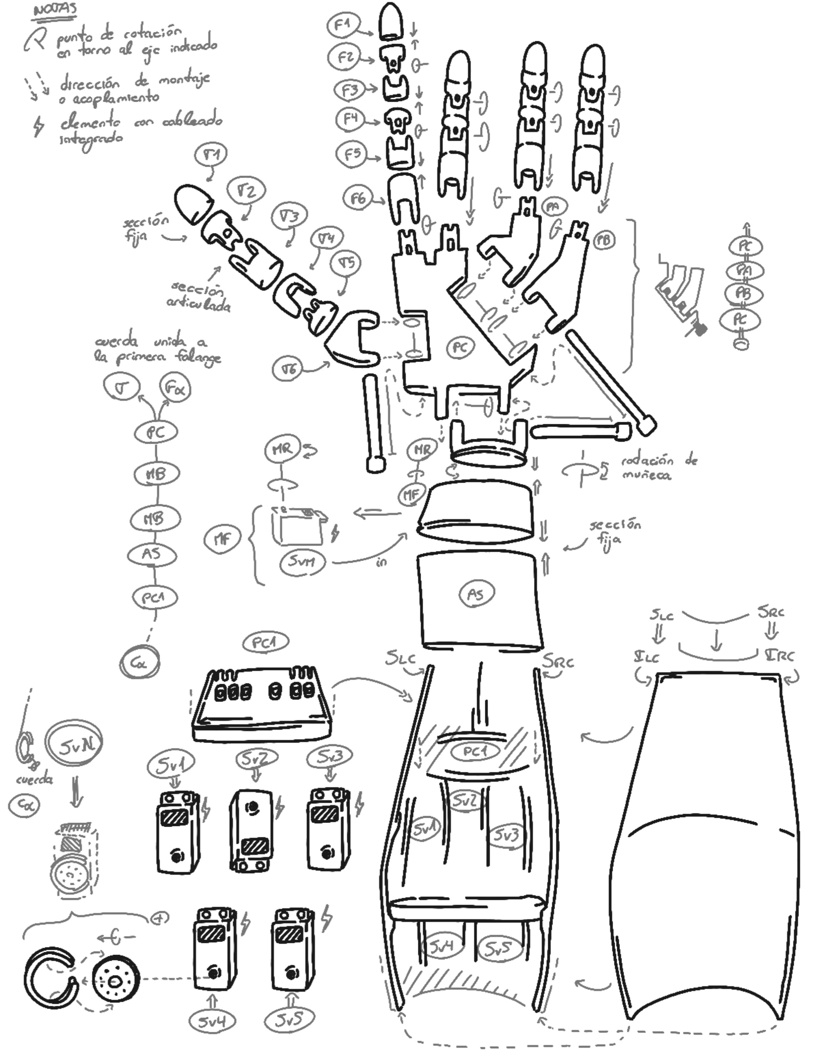
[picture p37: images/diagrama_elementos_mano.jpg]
diagrama

</div>

<div style="flex: 1;">
<table>
  <tr>
    <th>F1 - F6</th>
    <td>Falanges de la superior a inferior, de todo dedo salvo el pulgar</th>
  </tr>
  <tr>
    <th>T1 - T6</td>
    <td>Falanges de la superior a inferior, del dedo pulgar</td>
  </tr>
  <tr>
    <th>PA</td>
    <td>Pieza intermedia entre la parte central de la mano y el dedo anular. Esta pieza rota en torno a un tornillo que la encaja</td>
  </tr>
  <tr>
    <th>PB</td>
    <td>Pieza intermedia entre la parte central de la mano y el dedo meñique. Esta pieza rota en torno a un tornillo que la encaja</td>
  </tr>
  <tr>
    <th>PC</td>
    <td>Pieza central de la mano sobre la cual se ensamblan los dedos pulgar, índice y corazón, y las piezas intermedias PA y PB</td>
  </tr>
  <tr>
    <th>MR</td>
    <td>Parte rotativa de la muñeca, apoyada sobre la muñeca fija, y ofreciendo movimiento en torno al servomotor interno a la misma</td>
  </tr>
  <tr>
    <th>MF</td>
    <td>Muñeca fija, conjunto de piezas y cobertura que sirven de apoyo a la muñeca rotativa para ejercer su giro</td>
  </tr>
  <tr>
    <th>SVM</td>
    <td>Servomotor de la muñeca. Situado interno a la muñeca fija, y anclado a la rotativa</td>
  </tr>
  <tr>
    <th>AS</td>
    <td>Antebrazo superior. Conjunto de piezas encarcasadas más cortas que el antebrazo posterior, uniendo la muñeca con el mismo</td>
  </tr>
  <tr>
    <th>SLC & SRC</td>
    <td>Esquinas superior izquierda (SLC) y superior derecha (SRC) de la carcasa interna del antebrazo posterior o largo. Deben ir alineadas con ILC e IRC respectivamente</td>
  </tr>
  <tr>
    <th>ILC & IRC</td>
    <td>Esquinas superior izquierda (ILC) y superior derecha (IRC) de la carcasa externa del antebrazo largo. La carcasa de la que forman parte se alinea con la previamente mencionada y la recubre, dando forma al antebrazo</td>
  </tr>
  <tr>
    <th>PC1</td>
    <td>Conjunto de piezas centrales al antebrazo largo, ensambladas sobre la carcasa interna para servir de guía para los cables o fibras que mueven los dedos</td>
  </tr>
  <tr>
    <th>SV1 - SV6</td>
    <td>Servomotores numerados del 1 al 6, Componen el sistema de movimiento de los dedos de la mano, uniéndose a ellos por medio de unas cuerdas (C alpha) ancladas a los servos gracias a unas guías circulares</td>
  </tr>
  <tr>
    <th>SVN</td>
    <td>Abreviatura utilizada para referirse a "cualquier servomotor del antebrazo", pudiendo ser desde SV1 hasta SV6 pero no SVM</td>
  </tr>
  <tr>
    <th>C alpha</td>
    <td>Abreviatura utilizada para referirse a "cualquier cuerda ó fibra encargada de guiar el movimiento de los dedos desde su unión a un servomotor SVN" </td>
  </tr>
</table>
</div>

</div>

Aunque en el diagrama aparecen indicados también una serie de elementos que forman parte del dibujo, y la guía puede ser de ayuda para entender las abreviaturas, hay algunas cosas más que hay que tener en cuenta relativas al montaje: 
- Cada dedo está dividido en el mismo número de falanges, y cada falange cuenta con uniones tanto fijas como rotativas, indicadas estas últimas con un icono explicativo en la imagen superior.
- Las falanges de los dedos, tanto pulgar como índice, corazón, anular y meñique, cuentan con guías para los cables en las uniones articuladas, y con aberturas en aquellas uniones fijas, para que sea posible la unión entre la parte final de cada dedo y el servomotor que lo controlará.
- Además de los tornillos de ensamblaje que se han dibujado arriba, el montaje requirió de la utilización de otros tornillos metálicos no indicados previamente, así como algunos elementos adicionales para la correcta sujeción de algunas piezas.
- La parte interior del antebrazo largo, así como el antebrazo superior en detalle, que se indican previamente y se encuentran explicados, cuentan con otros elementos internos en su estructura, no mencionados por no ser de especial relevancia para la comprensión del funcionamiento del sistema mecánico que conforma la Mano de Zeus

### Esquematización

Queda a continuación un breve time lapse de la **parte final** del diseño del esquema superior:

time-lapse

### Impresión y ensamblaje

* Primeras impresiones.

A continuación se muestran la imagenes de las primeras impresiones de los ficheros stl que nos proporciona el proyecto original.

<div align="center">
  <a>
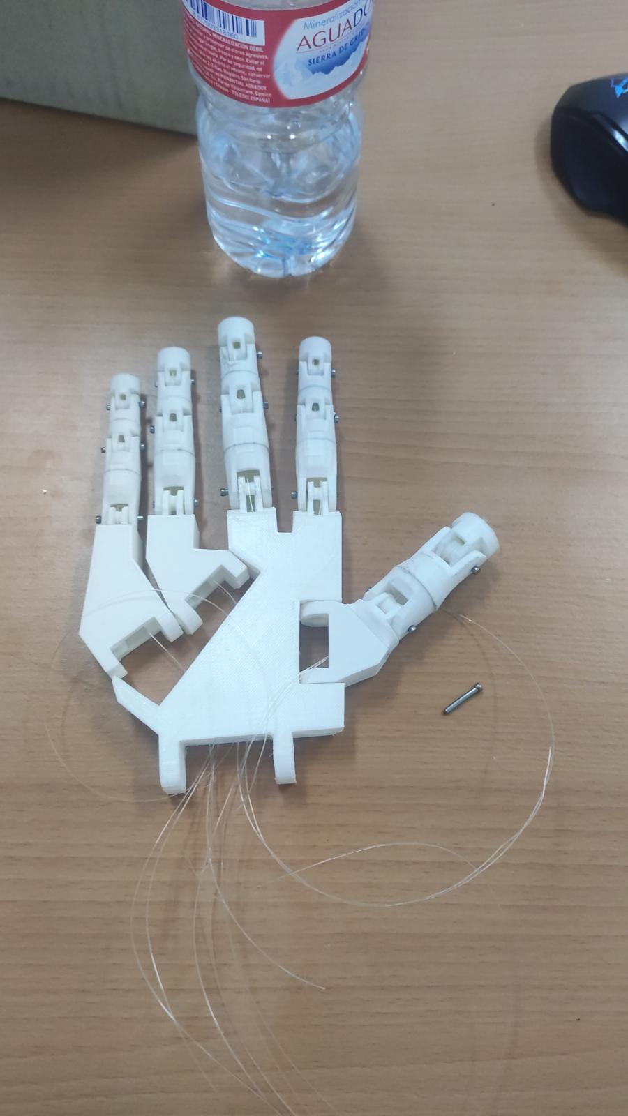
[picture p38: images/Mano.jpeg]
    
  </a>
 <a>
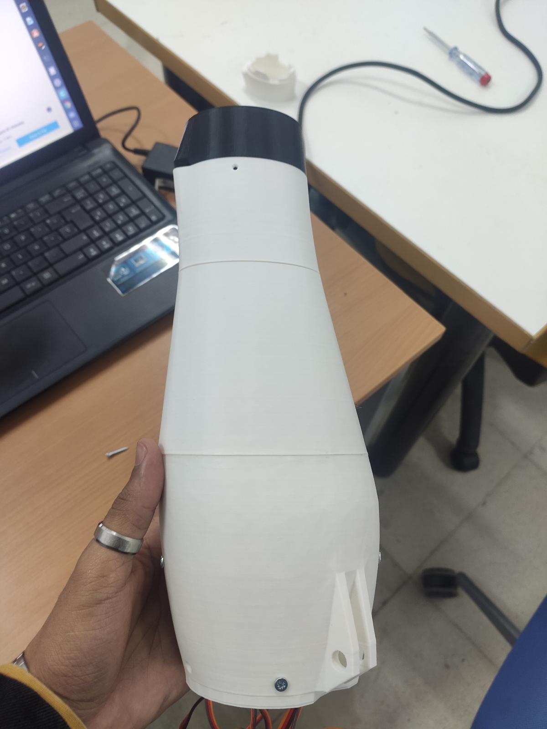
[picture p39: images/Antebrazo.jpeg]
    
  </a>
 <a>
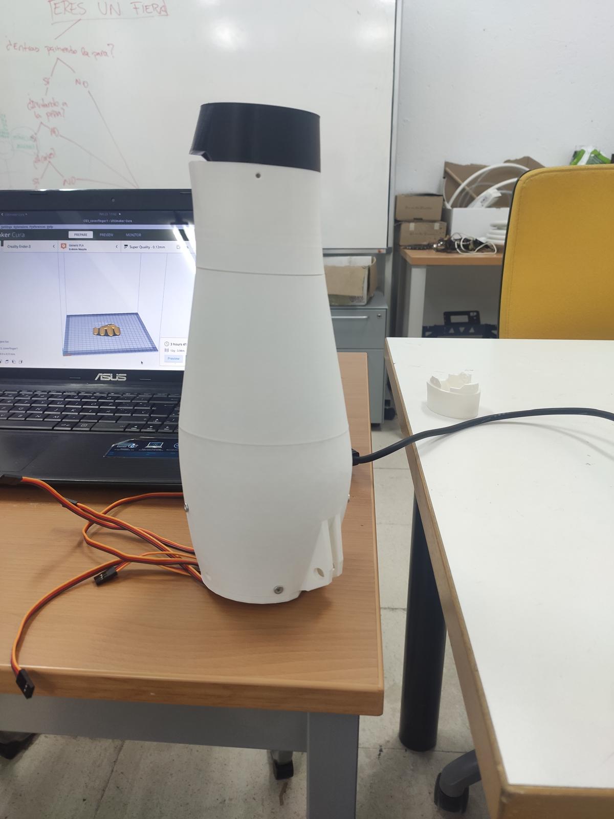
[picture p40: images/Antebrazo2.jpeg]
    
  </a>
 <a>
    
  </a>
  <a>
    
  </a>
  <a>
    
  </a>

</div>
La totalidad de las impresiones de han hecho en una impresora <a href="https://www.creality.com/es/products/ender-3-3d-printer"><strong>Creality Ender 3 »</strong></a>

* Problemas y dificultades.

El mayor problema de todos a la hora de montar las piezas es el material de las mismas, PLA. Esto provocaba que a la hora de encajar o generar una fuerza sobre ellas que no estaba
preparada para soportar, rompiamos la pieza. Han sido varias las piezas que se han vuelto a imprimir debido a roturas. 

Hay que tener en cuenta que hay muchas fricciones y tensiones simultaneas en el mecanismo completo de una sola mano, un total de 6 servos independientes que actuan para cada dedo y muñeca,
que esto funcione acorde es bastante importante, debido a que un minimo error puede provocar las roturas mencionadas anteriormente.

<div  id='id5' /> 

## Código de la Mano de Zeus

El código de la mano esta desarrollado en tres lenguajes, en C++, en Arduino y en Python. 

### Instalación 

Para que funcione correctamente el programa es necesario instalar previamente algunas librerías, a parte de los lenguajes usados.

Librerías utilizadas:

| Librerías | Comando de terminal  | Utilidad
|:--- |:---:| :---|
| numpy | pip install numpy | crear y usar vectores
| tkinter | pip install tkinter | crear una interfaz interactiva
| mediapipe | pip install mediapipe | detectar cuerpos, brazos y manos
| pillow | pip install pillow | procesar imagenes |

En cuanto al desarrollo del código de la mano, lo hemos dividido en varias partes:

### Movimiento

La primera de las partes es el movimiento de la mano. En esta, solo nos centramos en producir el movimiento de los dedos y la muñeca a partir del uso de servomotores. Esta parte está programada en Arduino y C++.

Para comenzar, intentamos entender cómo funcionaban nuestros servos. Estos se mueven al recibir un valor de 0 a 180, los cuales simbolizan velocidades. El valor 90 representa velocidad nula; por encima de este, el servo gira en sentido antihorario, y por debajo, en sentido horario.

Para probar el correcto funcionamiento de los servos, utilizamos un código simple que se encarga de girar los servos en ambos sentidos, de forma intercalada.

~~~
#include <Servo.h>

Servo myservo; 
int currentPos = 0;
int targetPos = 90;
int speedLeft = 80;
int speedRight = 100;
int stopSpeed = 90;

void setup() {
  myservo.attach(3);
  myservo.write(stopSpeed);
  delay(1000);
}

void loop() {
  targetPos = 180; 
  moveServoTo(targetPos);  
  
  targetPos = 0;
  moveServoTo(targetPos);
}

void moveServoTo(int targetPos) {
  if (targetPos > currentPos) {
    myservo.write(speedRight); 
  } else if (targetPos < currentPos) {
    myservo.write(speedLeft);
  }
  delay(2000);
  myservo.write(stopSpeed); 
  currentPos = targetPos;
}
~~~

Después creamos un código que mueve los servos por ángulos, estimando el tiempo que tarda en moverse de un ángulo a otro. A este código solo se le debe pasar el ángulo al cual se quiere ir, y moverá el servo lo necesario para llegar a esa posición. 

El código completo está en los documentos [ServoM.cpp](./src/ServoM/ServoM.cpp) y [ServoM.h](./src/ServoM/ServoM.h).

### Comunicación

Tras desarrollar el código de movimiento de los servos, nos preguntamos cuál es la mejor manera de comandar los movimientos. Para ello se nos ocurrieron diferentes ideas.

La primera fue usar una ESP32 y comunicarnos con ella a través de WiFi desde el ordenador. No obstante, esta idea la descartamos para los primeros pasos, ya que, aparte de no contar con una ESP32, no queríamos complicar más el código con una comunicación muy compleja. Además, conseguir la reactividad deseada nos costaría bastante. Sin embargo, el uso de una ESP32 y WiFi es una idea a desarrollar para el prototipo final.

La segunda fue el uso de la comunicación serial. Esta es la que hemos decidido usar, ya que es bastante sencilla de programar y nos da una reactividad muy elevada. Como único inconveniente, el Arduino debe estar conectado al ordenador; aunque, de momento, al tener el Arduino accesible, no es un problema.

Nuestra comunicación está programada en Arduino y es el programa que se encarga de recibir los ángulos de la parte de detección y pasárselos a la parte de movimiento. 

El código completo está en el documento [ServoM.ino](./src/ServoM/ServoM.ino)

### Detección

Después de conseguir un buen funcionamiento del movimiento de los servos y de la comunicación, nos planteamos de qué manera íbamos a detectar y elegir cuáles eran los ángulos que les pasaríamos a los servos. 

La primera idea que se nos ocurrió fue escribir los ángulos por teclado, la opción más simple, pero un poco lenta, ya que debíamos escribir los ángulos a mano constantemente y para cada servo. Por lo tanto, la descartamos de inmediato.

La siguiente idea fue, en lugar de escribirlos, desarrollar unos controles deslizantes para todos los servos y enviar el valor correspondiente. Este era un método sencillo y más rápido. No obstante, aunque no era lo suficientemente cómodo y rápido para el objetivo del proyecto, lo dejamos como una opción para pruebas, en un modo aparte.

<p align="center">
  detect_manual
</p>

Finalmente, después de pensarlo mucho, se nos ocurrió, a partir de una asignatura que cursamos llamada Visión Artificial, utilizar una cámara para obtener una imagen de nuestros brazos y, a partir de esa imagen, calcular los ángulos de los dedos. Esto nos permitía una detección constante y rápida. El único inconveniente era que era más complejo de desarrollar, aunque finalmente lo conseguimos.

<p align="center">
  detect_image
  detect_angles
</p>

La detección completa está programada en Python y se ejecuta desde el ordenador o dispositivo, al cual está conectado el Arduino por conexión Serial.

El código completo está en el documento [mano_zeus.py](./src/handTracking/mano_zeus.py)

### Interfaz

Para terminar, se nos ocurrio desarrollar una simple interfaz desde la cual el usuario pueda interactuar con el programa para así elegir que modo quiere y que parametros quiere que se muestren, mientras que este puede observar la detección en tiempo real y los angulos que se pasan al Arduino.

Esta parte también esta desarrollada en Python y esta es una imagen de la interfaz desarrollada:

<p align="center">
  interfaz
</p>

El código completo está en el documento [mano_zeus.py](./src/handTracking/mano_zeus.py)

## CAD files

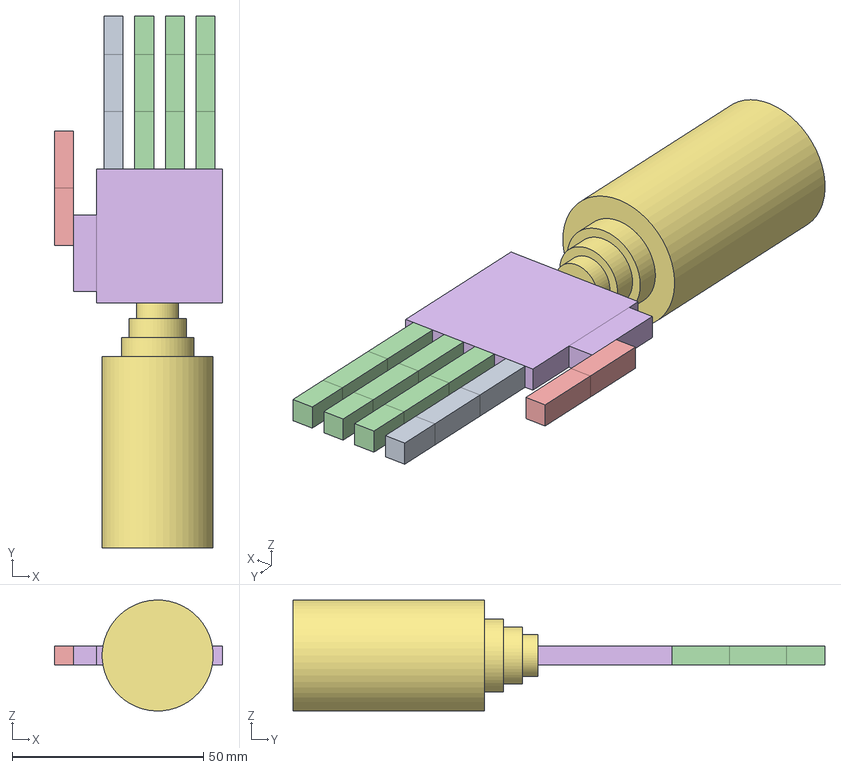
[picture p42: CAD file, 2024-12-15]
images/Mano.FCStd
44.0 x 139.0 x 29.0 mm
Connect
Connect001
Connect002
Connect003
Connect004
Connect005

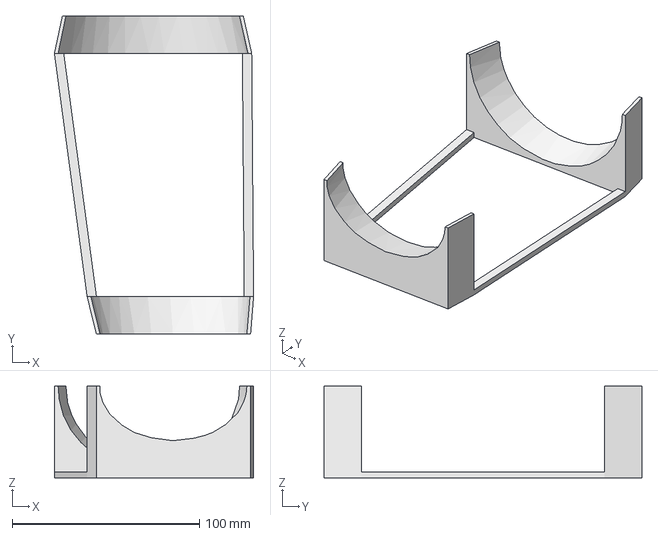
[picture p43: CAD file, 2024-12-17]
models/soporte_redu.FCStd
106.5 x 170.0 x 49.0 mm

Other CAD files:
models/soporte_redu.blend
models/soporte_redu.stl

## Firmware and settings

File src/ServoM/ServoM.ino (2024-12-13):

/*###########################################
## Author's github:    madport             ##
## Author's github:    vbarcena2020        ##
#############################################
*/

#include "ServoM.h"

enum
{
  NUMSERVOSHAND = 6,
  NUMHANDS = 2,
  NUMARMS = 0,
  NUMINVALUES = (NUMSERVOSHAND*NUMHANDS+NUMARMS),
  DIGITSPERVAL = 3,
};

int lpins[NUMSERVOSHAND] = {2, 3, 4, 5, 6, 7};
int rpins[NUMSERVOSHAND] = {8, 9, 10, 11, 12, 13};
// int armspins = {};
int acel = 200;

ServoM lservos[NUMSERVOSHAND] = {
  ServoM(acel, -180, 180),
  ServoM(acel, -180, 180),
  ServoM(acel, -180, 180),
  ServoM(acel, -180, 180),
  ServoM(acel, -180, 180),
  ServoM(acel*2, -180, 180)
};

ServoM rservos[NUMSERVOSHAND] = {
  ServoM(acel, -180, 180),
  ServoM(acel, -180, 180),
  ServoM(acel, -180, 180),
  ServoM(acel, -180, 180),
  ServoM(acel, -180, 180),
  ServoM(acel*2, -180, 180)
};

// ServoM larm = ServoM(acel*2, -180, 180);
// ServoM rarm = ServoM(acel*2, -180, 180);


int valsIn[NUMINVALUES];
int stringLenght = NUMINVALUES * DIGITSPERVAL + 1;
int counter = 0;
bool counterStart = false;
String recivedString;

void setup() 
{
  Serial.begin(9600);
  
  for (int i = 0; i < NUMSERVOSHAND; ++i) {
    lservos[i].attach(lpins[i]);
    rservos[i].attach(rpins[i]);
    lservos[i].write(90);
    rservos[i].write(90);
  }
  // rarm.attach(armspins[0]);
  // larm.attach(armspins[1]);
}

void receiveData()
{
  while(Serial.available())
  {
    char c = Serial.read();
    if (c=='$') {counterStart = true; }
    
    if (counterStart)
    {
      if (counter < stringLenght)
      {
        recivedString = String(recivedString+c);
        counter++;
      }
      if (counter >= stringLenght){

        for (int i = 0; i < NUMINVALUES ; i++){
          int num = (i*DIGITSPERVAL) + 1;
          valsIn[i] = recivedString.substring(num,num + DIGITSPERVAL).toInt();
          
        }
        // for (int i = 0; i < NUMINVALUES ; i++) {
        //   Serial.print(valsIn[i]);
        //   Serial.print(",");
        // }
        // Serial.println();
        recivedString = "";
        counter = 0;
        counterStart = false;
      }
    }
  }
}

void loop() 
{
  receiveData();
  // for (int i = 0; i < NUMSERVOSHAND; i++ ) {
  //   lservos[i].goTo(valsIn[i]);
  //   rservos[i].goTo(valsIn[i+NUMSERVOSHAND]);
  // }
  // larm.goTo(valsIn[NUMSERVOSHAND*2]);
  // rarm.goTo(valsIn[NUMSERVOSHAND*2+1]);

  // ------ left_hand positions -------
  // ------  right_hand positions -------

  // if (valsIn[1] == 1) {lservos[1].goTo(180);} 
  // else {lservos[1].goTo(1);}

  for (int i = 0; i < NUMSERVOSHAND; ++i) {
    if (valsIn[i] >= 90) {lservos[i].goTo(180);} 
    else {lservos[i].goTo(0);}

    if (valsIn[i + 6] >= 90) {rservos[i].goTo(180);} 
    else {rservos[i].goTo(0);}
  }
}

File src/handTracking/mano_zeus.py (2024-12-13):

#############################################
## github:    madport                      ##
## github:    vbarcena2020                 ##
#############################################

##############################################################################################
##                                                                                          ##
## You have to select how many hands you want and if it is only one wich one example        ##
##                                                                                          ##
## Usage: python3 mano_zeus.py --n 2            # detect two hands                          ##
##                                                                                          ##
## Usage: python3 mano_zeus.py --n 1            # detect one hand                           ##
##                                                                                          ##
##############################################################################################

import cv2
import mediapipe as mp
import time
import serial
import sys
import numpy as np
import symbols
import tkinter as tk
from PIL import Image, ImageTk


PORT = '/dev/ttyACM0'
SERIALBEGIN = 9600
INIT_CHAR = "$"

COLOR_LETTERS = (255, 255, 255)
COLOR_USED = (255, 0, 255)

RATIO_NODES = 4

USED_ARM_NODES = [11, 12, 13, 14, 15, 16]

THUMB_FINGER = 4
INDEX_FINGER = 8
MIDDLE_FINGER = 12
RING_FINGER = 16
PINKY_FINGER = 20

LEFT = 0
RIGHT = 1

LEFTSTRING = "Left"
RIGHTSTRING = "Right"
NAMES = ["Thumb:  ", "Index:  ", "Middle: ", "Ring:   ", "Pinky:  ", "Wrist:  ", "Elbow:  "]

REFERENCE_INIT = 0
REFERENCE_THUMB = 5
REFERENCE_MIDDLE = 9
REFERENCE_UPPER = 13
REFERENCE_WRIST = 17

NODES_FINGERS = [(4, 8, 12, 16, 20), (5, 5, 9, 13, 17), (17, 0, 0, 0, 0)]

USED_FACE_NODES = [0, 1, 2, 3, 4, 5, 6, 7, 8, 9, 10]

manualangles = [180, 180, 180, 180, 180, 180, 180, 180, 180, 180, 180, 180, 180, 180]

traces = False
arms = True
mode = 0
root = tk.Tk()


class Interface:
    def __init__(self, root):
        self.root = root
        self.root.title("Interface Mano Zeus")

        # Create two areas to show images
        self.img_label1 = tk.Label(self.root)
        self.img_label1.pack(side="left", padx=10, pady=10)

        self.img_label2 = tk.Label(self.root)
        self.img_label2.pack(side="right", padx=10, pady=10)

        # Create label
        self.l = tk.Label(root, text = "CHANGE MODE")
        self.l.config(font =("Courier", 20, "bold"))
        self.l.pack(side="top", pady= 5)

        self.l_2 = tk.Label(root, text = "MODE" + str(mode+1), fg="blue")
        self.l_2.config(font =("Courier", 15, "bold"))
        self.l_2.pack(side="top", pady= 5)

        # Buttons
        self.button1 = tk.Button(self.root, text="Mode 1: SYMBOLS", command=self.button_mode1)
        self.button1.pack(side="top", pady=5)

        self.button2 = tk.Button(self.root, text="Mode 2: HANDS", command=self.button_mode2)
        self.button2.pack(side="top", pady=5)

        self.button3 = tk.Button(self.root, text="Mode 3: FACE", command=self.button_mode3)
        self.button3.pack(side="top", pady=5)

        self.button4 = tk.Button(self.root, text="Mode 4: MANUAL", command=self.button_mode4)
        self.button4.pack(side="top", pady=5)

        self.label_manual = tk.Label(self.root, text = "MANUAL MODE")
        self.label_manual.config(font =("Courier", 20, "bold"))
        self.label_manual.pack(side="top", pady= 5)

        self.buttonmove = tk.Button(self.root, text="MOVE", command=self.button_move)
        self.buttonmove.pack(side="top", pady=5)

        self.slider_frame = tk.Frame(self.root)
        self.slider_frame.pack()

        left_label = tk.Label(self.slider_frame, text="LEFT")
        left_label.grid(row=0, column=1)
        
        right_label = tk.Label(self.slider_frame, text="RIGHT")
        right_label.grid(row=0, column=2)

        # Crear 12 sliders y organizarlos en dos columnas de 6 dentro del frame
        self.sliders = []
        for i in range(12):
            if i < 6:
                # Colocar las etiquetas con números a la izquierda de los sliders
                tk.Label(self.slider_frame, text=str(NAMES[i])).grid(row=i + 1, column=0)

            slider = tk.Scale(self.slider_frame, from_=0, to=180, orient=tk.HORIZONTAL, troughcolor="red")
            slider.set(180)  # Establecer valor inicial en 180
            self.sliders.append(slider)
            # Colocarlos en una cuadrícula: 6 filas y 2 columnas dentro del frame
            slider.grid(row=(i % 6) + 1, column=(i // 6) + 1)

        self.label_manual = tk.Label(self.root, text = "OTHERS")
        self.label_manual.config(font =("Courier", 20, "bold"))
        self.label_manual.pack(side="top", pady= 5)

        self.buttontraces = tk.Button(self.root, text="Show/hide traces", command=self.button_traces)
        self.buttontraces.pack(side="top", pady=5)

        self.buttonarms = tk.Button(self.root, text="Show/hide arms", command=self.button_arms)
        self.buttonarms.pack(side="top", pady=5)

        self.buttonexit = tk.Button(self.root, text="EXIT", command=self.button_exit)
        self.buttonexit.pack(side="top", pady=5)

    def button_move(self):
        global mode, manualangles
        if mode == symbols.MANUAL_MODE:
            values = [slider.get() for slider in self.sliders]
            values.append(180)
            values.append(180)
            print(f"Valores actuales de los sliders: {values}")
            manualangles = values
        else:
            print("Manual mode not active")

    def update_sliders(self):
        if mode == symbols.MANUAL_MODE:
            i = 0
            for slider in self.sliders:
                if slider.get() == manualangles[i]:
                    slider.config(troughcolor="green")
                else: 
                    slider.config(troughcolor="yellow")
                i = i+1
        else:
            for slider in self.sliders:
                slider.config(troughcolor="red")
        self.root.update_idletasks()


    def update_images(self, img1, img2):    
        img1_rgb = cv2.cvtColor(img1, cv2.COLOR_BGR2RGB)
        img2_rgb = cv2.cvtColor(img2, cv2.COLOR_BGR2RGB)

        self.img1 = ImageTk.PhotoImage(Image.fromarray(img1_rgb))
        self.img2 = ImageTk.PhotoImage(Image.fromarray(img2_rgb))

        self.img_label1.config(image=self.img1)
        self.img_label2.config(image=self.img2)

        self.root.update_idletasks()
    
    def update_text(self):
        global mode
        
        # Mostrar las imágenes en las etiquetas
        self.l_2.config(text="MODE " + str(mode+1))

        self.root.update_idletasks()

    def button_mode1(self):
        global mode
        mode = 0

    def button_mode2(self):
        global mode
        mode = 1

    def button_mode3(self):
        global mode
        mode = 2
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

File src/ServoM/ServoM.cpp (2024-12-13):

/*###########################################
## Author's github:    madport             ##
#############################################
*/
#include "ServoM.h"
#include "Arduino.h"


ServoM::ServoM(float time_turn, int min_pos, int max_pos)
{
  this->write(STOP_);
}

void ServoM::moveServoTo() {
  if (!turning_) return; // No hacer nada si no se está moviendo

  unsigned long currentMillis = millis(); // Tiempo actual

  if (currentMillis - moveStartTime < moveTime) {
    // Si todavía no hemos alcanzado el tiempo necesario, mantenemos el movimiento
    if (targetPos > currentPos) {
        this->write(LEFT_); // Girar a la derecha
    } else if (targetPos < currentPos) {
        this->write(RIGHT_); // Girar a la izquierda
      }
  } else {
    // El tiempo de movimiento ha terminado, detener el servo
    this->write(STOP_);
    currentPos = targetPos; // Actualizar la posición actual
    turning_ = false;       // Finalizar el movimiento
  }
}

unsigned long ServoM::estimateMoveTime(int start, int end) {
  int angleDifference = abs(end - start);
  return map(angleDifference, 0, 180, 0, 1000); // Suponemos que tarda 500 ms en moverse 180 grados
}

void ServoM::turn() {
   // Calcula el tiempo necesario para el movimiento
  turning_ = true;
  moveServoTo();                                   // Activa el estado de movimiento
}

void ServoM::goTo(double grades) {
  if (!turning_) {
    targetPos = grades;
    moveTime = estimateMoveTime(currentPos, targetPos);
    moveStartTime = millis();
  }
  turn(); // Inicia el movimiento hacia la posición objetivo

}

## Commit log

2024-11-24 3D design
    [Mano.FCStd]
2024-12-06 Update README.md
    eliminado el texto repetido
2024-12-07 readme actualizado con el esquema
2024-12-07 readme actualizado con el esquema 2
2024-12-13 add battery image
    [Mano.FCStd]
2024-12-15 3d hand design
    [Mano.FCStd]
2024-12-17 blender y freecad
    [soporte_redu.FCStd, soporte_redu.blend, soporte_redu.stl]
2024-12-17 cambio de sitio
